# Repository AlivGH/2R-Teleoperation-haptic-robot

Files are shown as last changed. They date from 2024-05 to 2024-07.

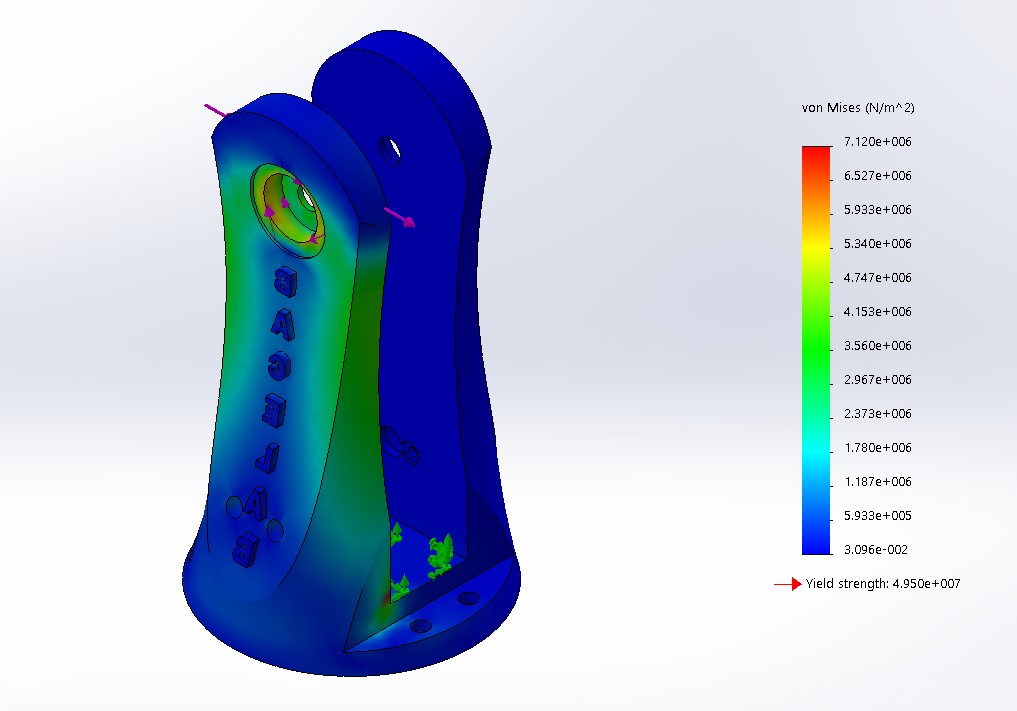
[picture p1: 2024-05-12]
Pictures/0-Tension-v2.jpg

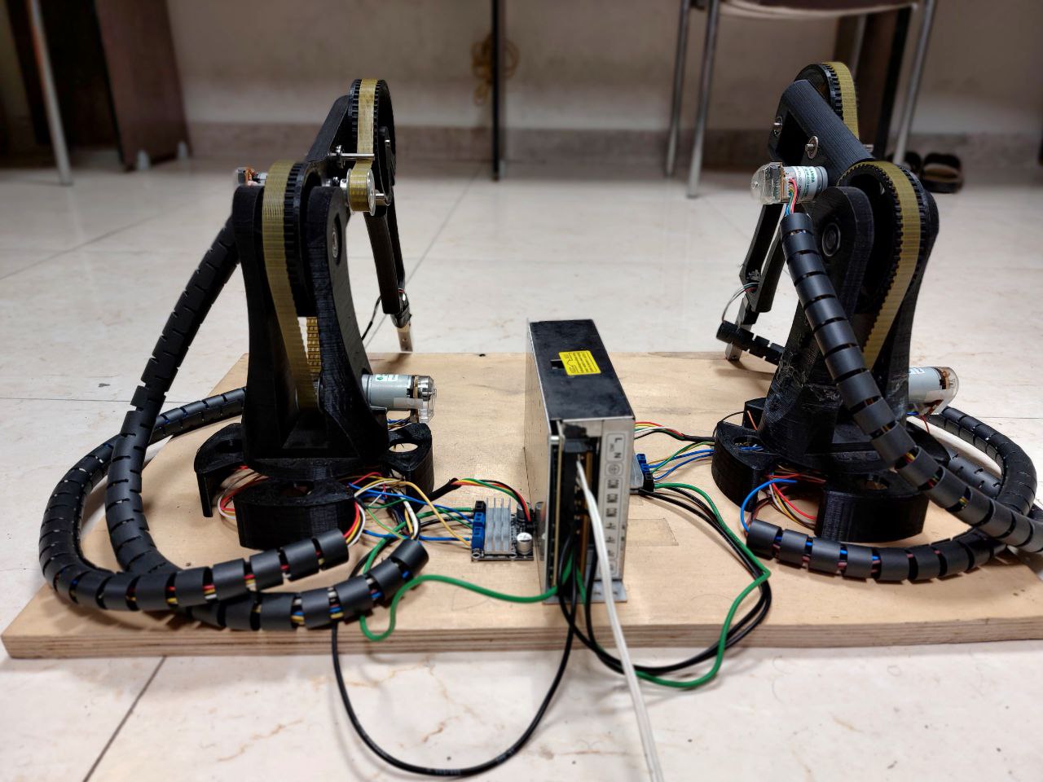
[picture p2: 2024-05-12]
Pictures/photo_5789467008948092437_y.jpg

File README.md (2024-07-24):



# Project Overview

Welcome to my GitHub repository! 🚀 Currently available haptic/teleoperation frameworks either are expensive, provide low-range haptic feedback, or lack sufficient rotational degrees of freedom. To tackle these drawbacks, this project introduces an economical teleoperation setup, including two robots serving as master and slave. The system is actuated by encoder-equipped DC motors, and the applied forces are measured by load cells at the end effectors of the robots. ESP WROOM-32D boards are also used for time-delayed wireless communication. 

The manipulators are first designed in SolidWorks and then printed using a 3D printer. Stress and deformation analyses under a 5-kg load are also provided. The cost-effectiveness of the proposed system is highlighted by reporting the relatively low manufacturing costs. Furthermore, the technical specifications of our framework demonstrate its appeal as an alternative to current haptic devices, offering affordability and versatility.

In this project, basic electrical and mechanical aspects (design, analysis, and manufacturing) are reviewed. For additional information, you can refer to my paper titled “[Cost-effective Haptic Teleoperation Framework: Design and Implementation](https://www.researchgate.net/publication/377825397_Cost-effective_Haptic_Teleoperation_Framework_Design_and_Implementation).”

## Key Skills

- Robotics 💻
- Design 🧠
- 3D Printing 🛠️
- SolidWorks

## Contact Information

Feel free to reach out to me via:

📫 Email: [alivghasemi@gmail.com](mailto:alivghasemi@gmail.com)

✏ LinkedIn: [Ali Ghasemi](https://www.linkedin.com/in/alivghasemi/)

Thank you for exploring my project! 🙌 Your feedback and contributions are highly appreciated. Let's continue pushing the boundaries of deep learning together! 🚀

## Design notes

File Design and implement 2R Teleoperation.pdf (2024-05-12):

## Design and implement

## a 2R Teleoperation haptic robot

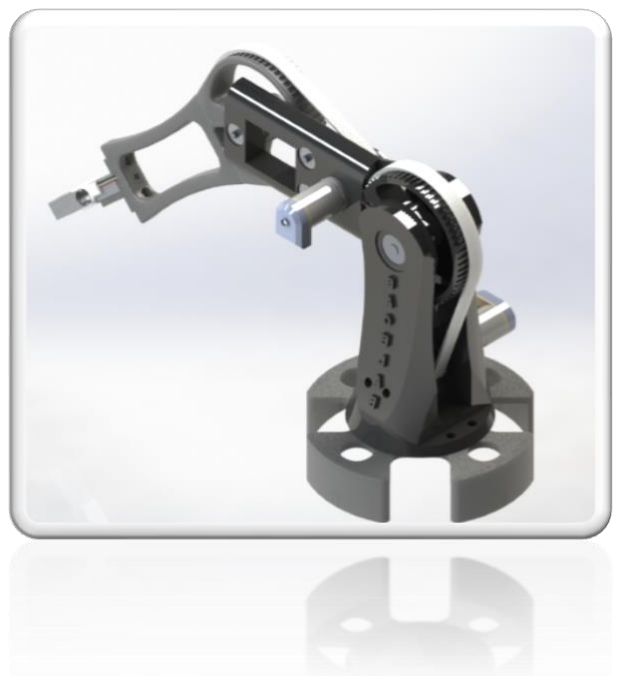
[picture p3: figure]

Ali Ghasemi

Mechanical Engineering Student

Research Enthusiast in Robotics and AI

Iran University of Science and Technology

Contents

## Abstract

Currently available haptic/teleoperation frameworks either are expensive, provide low-range haptic feedback, or lack sufficient rotational degrees of freedom. To tackle these drawbacks, this paper introduces an economical teleoperation setup, including two robots, serving as master and slave. The system is actuated by encoder-equipped DC motors, and the applied forces are measured by loadcells at the end effectors of the robots. ESP WROOM-32D boards are also used for time-delayed wireless communication. The manipulators are first designed in SolidWorks, and are then printed using a 3D printer. The stress and deformation analyses under a 5-kg load are also provided. The cost-effectiveness of the proposed system is highlighted by reporting the relatively low manufacturing costs. Furthermore, the technical specifications of our framework demonstrate its appeal as an alternative to current haptic devices, offering affordability and versatility.

In this project, Basic electrical and mechanical aspects (design, analysis, and manufacturing) are reviewed. However, if you are exploring additional information, you can refer to my paper titled “Cost-effective Haptic Teleoperation Framework: Design and Implementation”.

Key Skills: SolidWorks, Design, 3D printing, Robotics

## Introduction

What is haptic teleoperation robot?

A haptic teleoperation robot combines teleoperation with haptic feedback, providing the operator with a sense of touch or force feedback during remote control operations. This means that in addition to controlling the robot's movements remotely, the operator can also feel the forces exerted by the robot on its environment or objects it interacts with.

Haptic teleoperation systems typically involve force sensors or other feedback mechanisms that transmit the forces experienced by the robot to the operator's control interface. This allows the operator to perceive and react to the physical properties of the remote environment, such as the texture of surfaces or the resistance encountered when manipulating objects.

These systems are valuable in various applications, including surgery, where surgeons can remotely perform delicate procedures with a sense of touch, or in tasks involving hazardous environments, where operators can manipulate objects safely from a distance while receiving tactile feedback about the environment.

Overall, haptic teleoperation robots enhance the operator's control and perception, enabling more intuitive and effective remote operation in a wide range of scenarios.

Why we are creating one?

The current availability of affordable haptic devices presents a challenge: they tend to be either too expensive or difficult to reproduce outside specialized laboratories. This lack of affordable options has drawn attention, prompting a call for solutions that offer accessibility without sacrificing quality.

Commercially available haptic devices, while valuable, often come with limitations. For instance, the Phantom Omni device has a restricted force range, making it less suitable for tasks requiring interaction with rigid external environments or providing extensive haptic feedback.

In response to these challenges, there's a growing need for a teleoperation setup that balances affordability with functionality. Many attempts have been made to adapt existing haptic devices like the Novint Falcon due to their cost-effectiveness. However, this approach presents its own hurdles.

The Novint Falcon, though budget-friendly, lacks rotational degrees of freedom crucial for implementing certain teleoperation theories, limiting its applicability. Furthermore, as it's no longer in production, scalability and further development of systems based on it are slowed down.

In light of these limitations, our objective is to develop a teleoperation system that meets the diverse needs of research while remaining cost-effective. Our contribution lies in creating a framework that not only addresses affordability but also offers wide-range haptic feedback, ample workspace, and intuitive operation for the user.

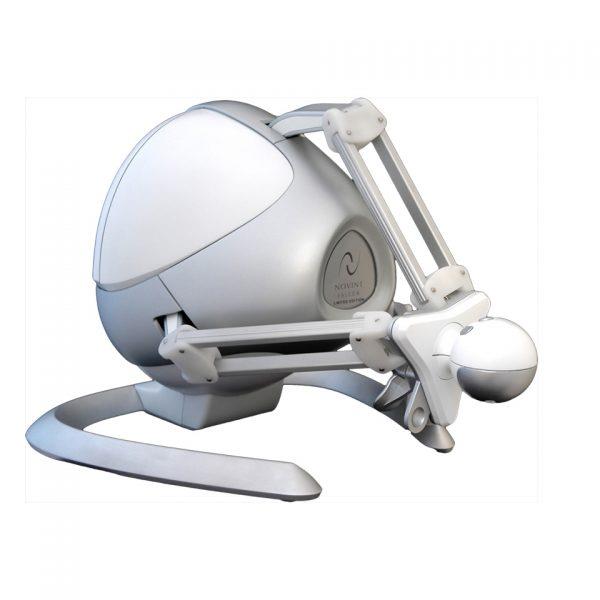
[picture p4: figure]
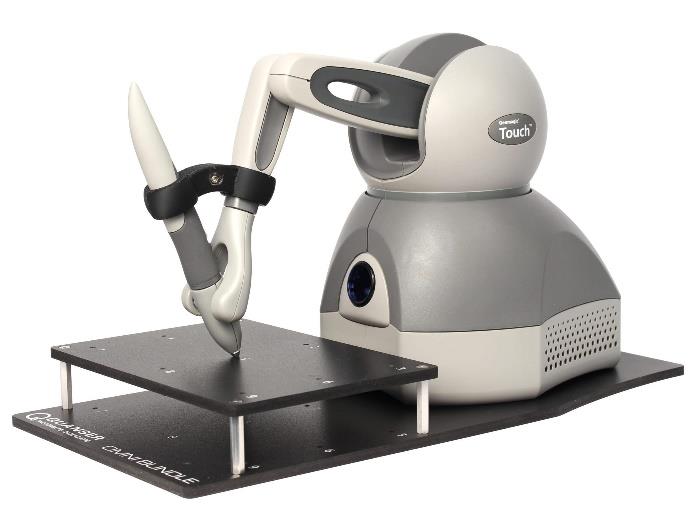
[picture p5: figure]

Figure 1: Falcon Haptic Device | Figure 2: Sensable Phantom

## Design of the system

The main focus of this study is design and construction of two identical 2-DoF robotic arms, the combination of which will form an experimental setup for teleoperation. We started designing the links in SolidWorks considering making the setup as light as possible. The examination of the system’s inertia is an outstanding concern, due to the significant disadvantages associated with excessive mass. To begin with, as the system becomes heavier, it requires more torque from the motors, which increases the overall setup cost. In addition, a heavier setup presents challenges in moving the master robot for the operator. To address this, we removed any surplus material in areas where it was considered unnecessary, ensuring the structural strength remains unquestioned. Furthermore, we determined the length of the links in a way to provide adequate workspace coverage without being overly large which results in mass increasing. The engineering drawings of the links for one robot are shown in Fig. 3. The 3D view of the assembled robot in SolidWorks is also shown in Fig. 4.

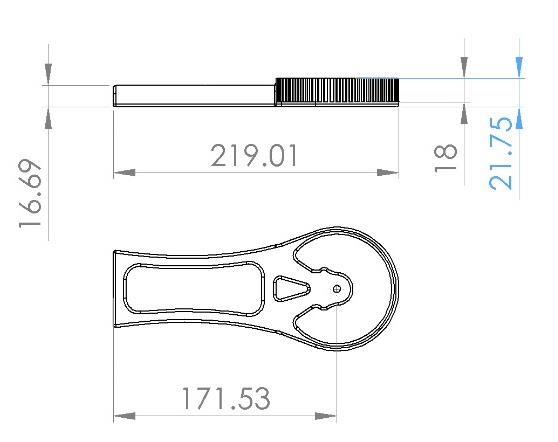
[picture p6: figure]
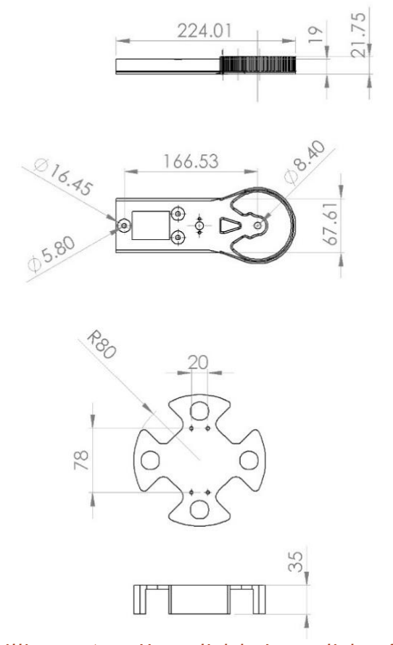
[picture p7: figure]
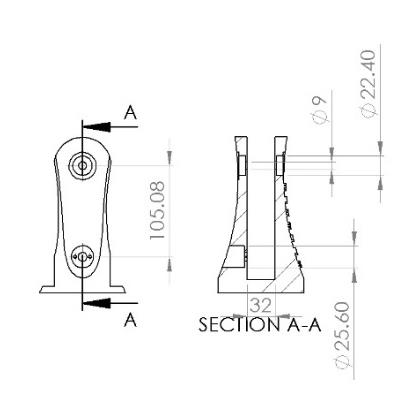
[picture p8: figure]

Figure 3: Drawings of the links of each robot (dimentions are in millimeters): a. Upper link b. Lower link c. Base link d. Base of the robot.

Due to the fact that all links will be produced using BACE lab’s 3D printer, it is essential to acknowledge and account for any constraints and limitations inherent to the printer.

To accommodate the installation of 2 DC motors, two circular empty spaces are incorporated into the robot base and lower link, with essential supports embedded within.

Given the high speed of our motors, power transmission is achieved through a combination of belts and gears. The gear ratio of 1/5 ensures that for every 5 rotations of the pulleys and motors, there is 1 rotation in the subsequent link. This results in the conversion of undesired high speed into torque, enabling a wider range of haptic forces.

As belts are utilized, it is imperative to ensure proper tension. To achieve this, shafts and ball bearings are employed.

The load cell is a vital component of the setup. We have developed a new T-shaped 3D element, called the load cell holder, which securely fastens the 5kg load cell to the robot link. This allows for precise measurement of the force applied on the slave robot, with feedback relayed to the master to mitigate potentially damaging effects.

Links are interconnected using shafts and ball bearings, enabling convenient movement with minimal friction.

In addition to the base support and two links, a base is provided beneath all parts for three primary reasons. Firstly, it elevates the entire setup, facilitating a broader range of operations. However, this elevation also introduces additional safety considerations. Secondly, with the inclusion of electrical units, providing a designated space minimizes confusion associated with complex wiring. Lastly, this base also lays the groundwork for expanding Degrees of Freedom (DoFs) to 3R, enhancing the versatility of the system.

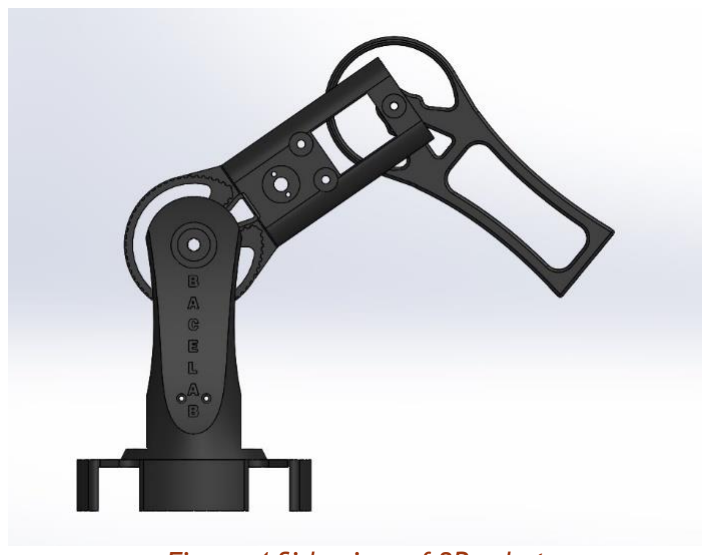
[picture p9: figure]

Figure 4 Side view of 2R robot

## Analysis of the system

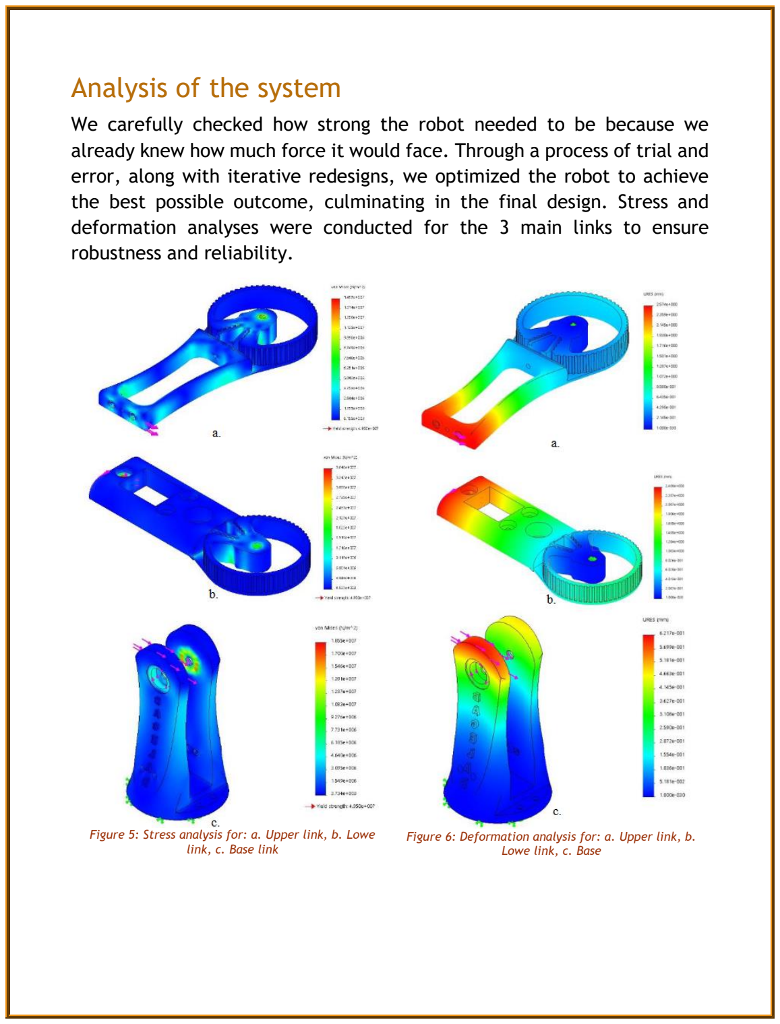
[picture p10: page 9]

We carefully checked how strong the robot needed to be because we already knew how much force it would face. Through a process of trial and error, along with iterative redesigns, we optimized the robot to achieve the best possible outcome, culminating in the final design. Stress and deformation analyses were conducted for the 3 main links to ensure robustness and reliability.

Figure 5: Stress analysis for: a. Upper link, b. Lowe link, c. Base link

Figure 6: Deformation analysis for: a. Upper link, b. Lowe link, c. Base

## Manufacturing of the system

Print Parts

In the beginning we start with printing components. We are using BACE lab 3D printer built by students and this printer use PLA(Polylactic Acid) as Material. To make G-code and also determine mechanical properties “UltiMaker Cura” Software is used.

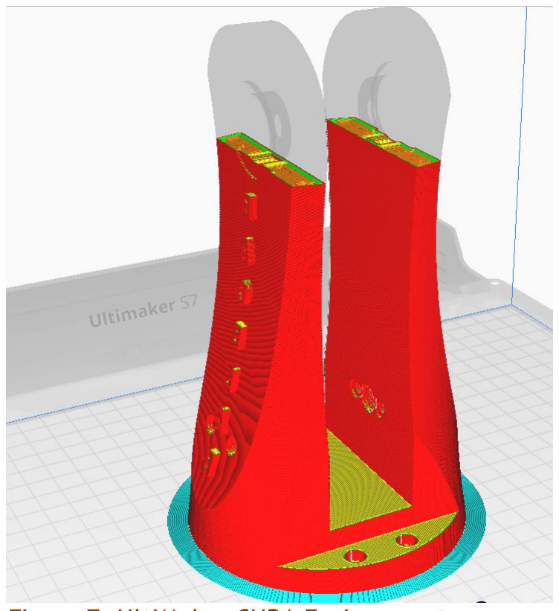
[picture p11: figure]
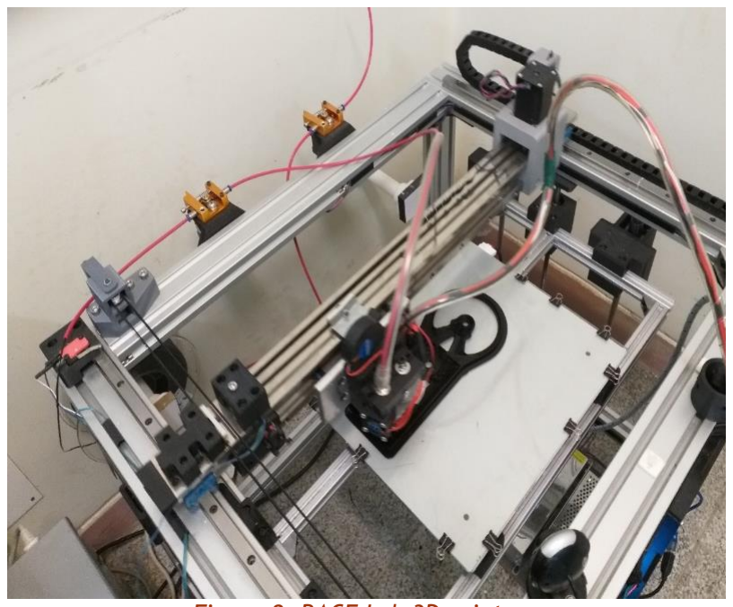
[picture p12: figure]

Figure 7: UltiMaker CURA Environment | Figure 8: BACE Lab 3D printer
All Components Designed in Solidworks Must be exported as <.STL> files. Then, Cura will modify print setting and finally create a G-Code. In the end of this process printer will construct parts. Whole .STL files are placed in GitHub Repository (https://github.com/AlivGH/2R-Teleoperation-haptic-robot) .

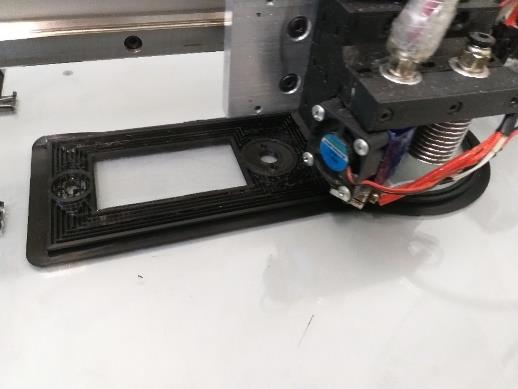
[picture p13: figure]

Figure 9: Printing Link 1

Mechanical properties and bill of material

Properties of designed teleoperation robot is given in following table

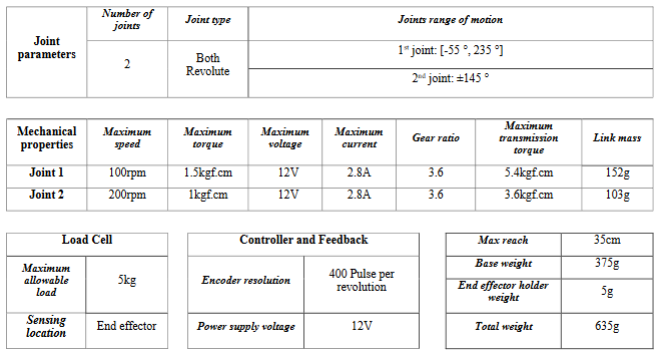
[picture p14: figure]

Other components:

DC Motor Driver | 1
Pulley T5 16teeth | 2
Belt T5 | 2
5mm shaft | 3
8mm shaft | 1
Ball bearing 8*22*7 | 2
Ball Bearing 5*16*5 | 6
Screw | 10 ( suitable size for bore )

Based on Estimation you can attempt to create this robot in USA 50$ and in Iran you can effort 30 million rial.

Setting up links

Base: We accommodated 2 hole for ball bearing and 8mm shaft. Also screw must be used to fix the Dc motor with robot. Pay a lot of attention to this affair. Then put pully on the Motor.

Link1: There are 3 bore in each side for 16mm diameter ball bearing. All 6 ball bearing are to support shafts. 1 shaft linking to next link and 2 utilizing as belt tighten. Put DC motor and then screw it to link. After that place pully on motor shaft.

Link2: 5mm hole to connect to Link1 and 2 holes to connect end effector

Put all together

First of all adjoin belt to links’ gear. Second via 8mm and 5mm shaft make links and base coupled . Then put belt around the pullies and for link 2 and 1 set up belt tighten. Do not forget the end effector and screw it to the holes of link2. Then, locate load cell on it. You also can leverage wire cover and improve the wiring more efficient. Base support can be added to system too.

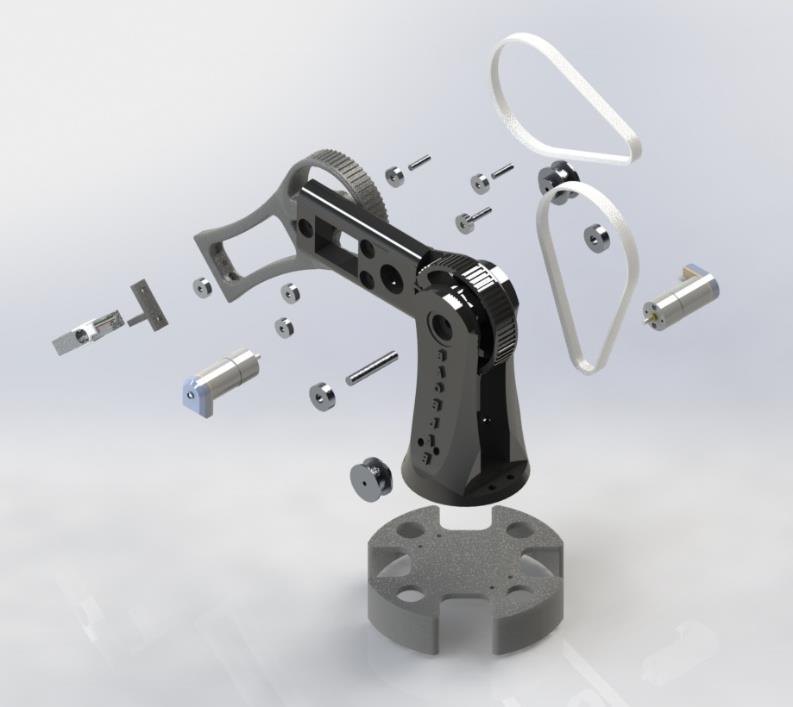
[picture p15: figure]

Figure 10: Exploded View

## Extension To 3R

As mentioned in sections II and III, we have constructed two 2-DoF robotic arms. However, a third degree of freedom can be added to each manipulator so that the three-dimensional space within the workspace of the robots can be reached. Although we have not yet implemented the third DoF, we have conceptualized and designed it in SolidWorks. The scheme of the complete 3-DoF robot is depicted in Fig. 9

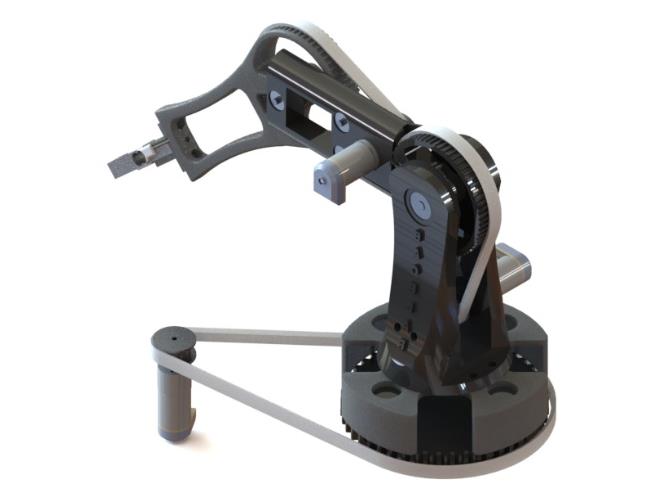
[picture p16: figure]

Figure 11 The 3D view of designed 3-DoF robot

## Make it a Teleoperation Robot

To turn your described robot into a teleoperation robot, you can build two of them and establish a suitable communication protocol. Based on our experience, we recommend using ESP32, which can transmit data through various methods and is cost-effective. Additionally, you'll need a DC motor driver (ZK-BM1), a power supply, wires, and a PerfBoard. You can refer to our paper for detailed methods and results.

## Acknowledge

A heartfelt shoutout to all the members of the Biomechatronic and Cognitive Engineering Lab at IUST, especially

Dr. Borhan Beig Zadeh

Dr. Behnam Yazdan Khoo

Mohammad Yousefi

Kiana Yousefi

Without their advice and generous help, manufacturing this robot would have been impossible. Their contributions were invaluable to the success of this project.

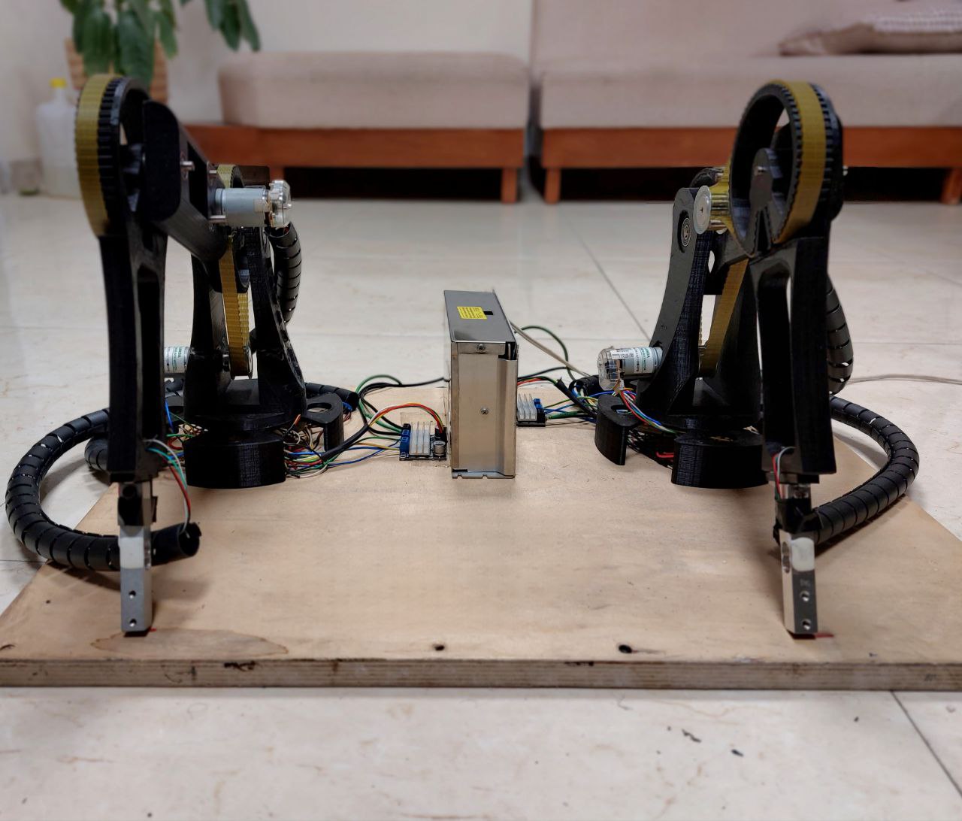
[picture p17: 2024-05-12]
Pictures/photo_5816758060075564648_y (1).jpg

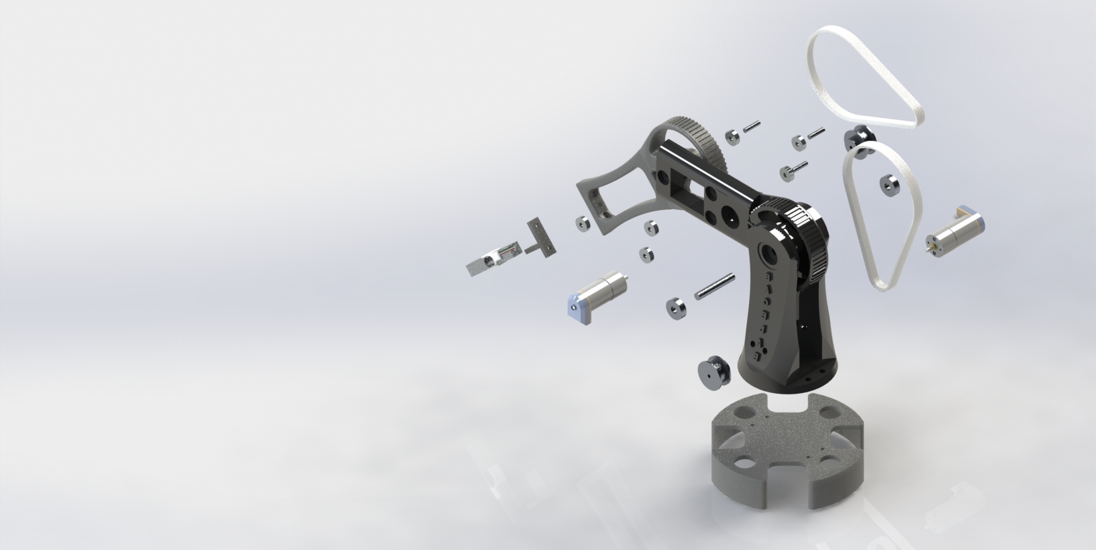
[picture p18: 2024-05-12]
Pictures/Expolded-2R.JPG

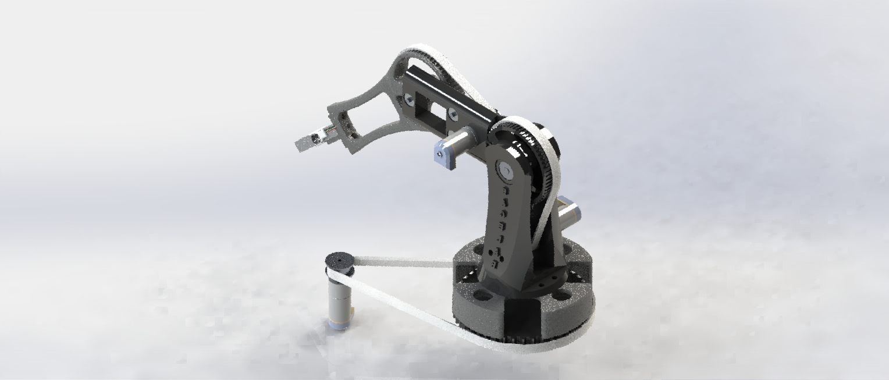
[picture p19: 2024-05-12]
Pictures/preview-3R-V2.JPG

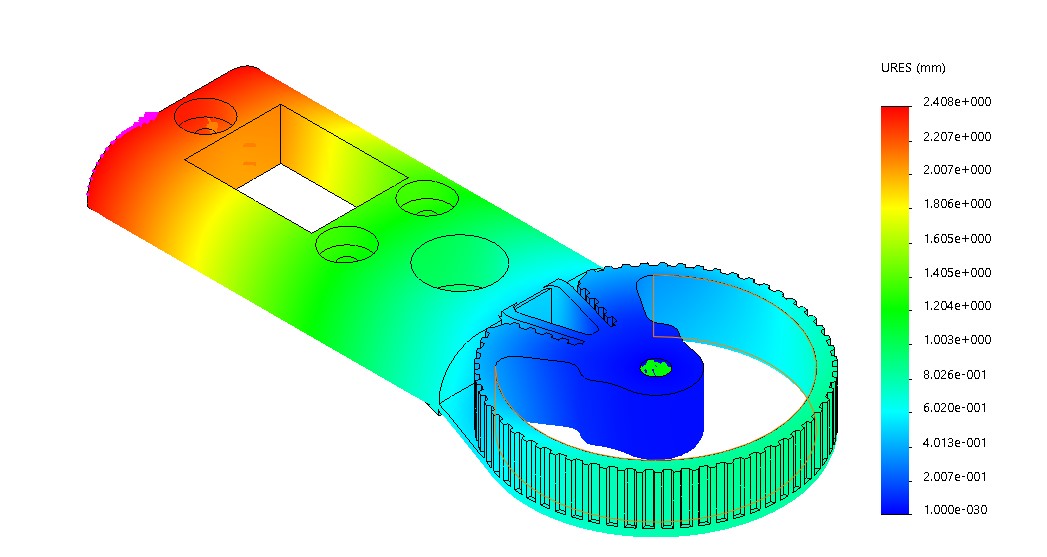
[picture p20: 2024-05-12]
Pictures/1-Strain-v3.jpg

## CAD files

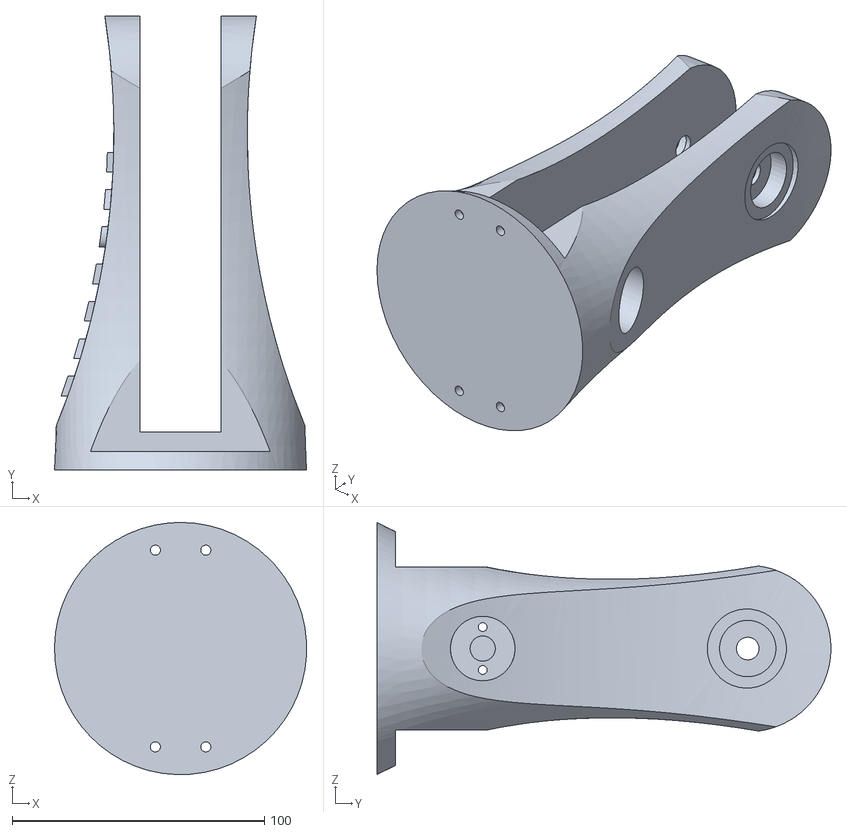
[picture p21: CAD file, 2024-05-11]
STL Files/Base.STL
99.9 x 180.0 x 100.0

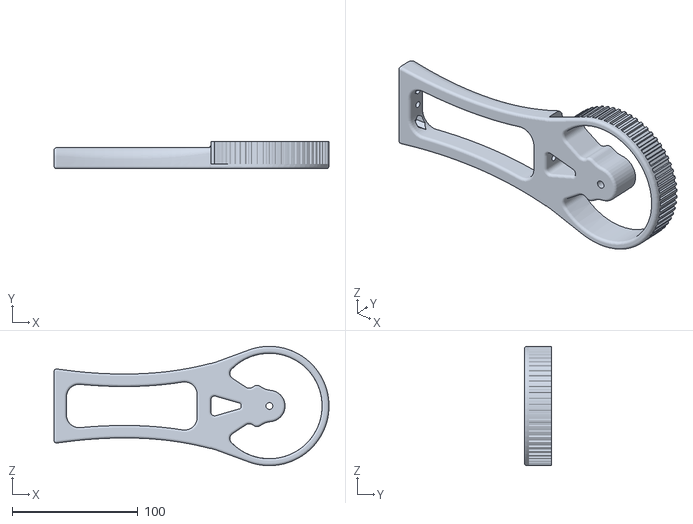
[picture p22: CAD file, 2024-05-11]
STL Files/Link2.STL
219.0 x 21.8 x 95.0

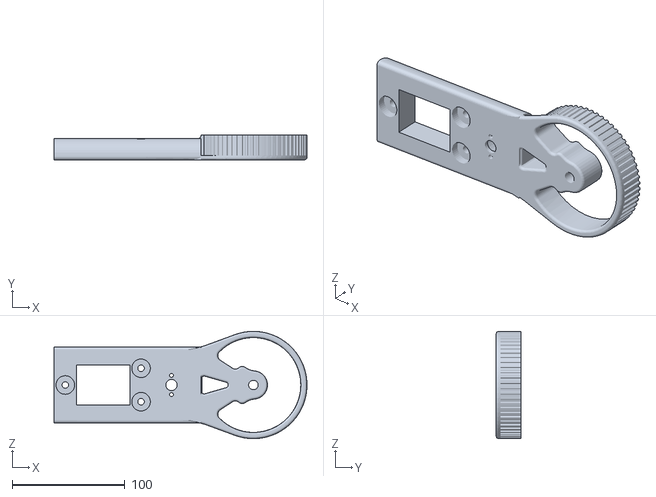
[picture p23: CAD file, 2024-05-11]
STL Files/Link1.STL
224.0 x 21.8 x 95.0

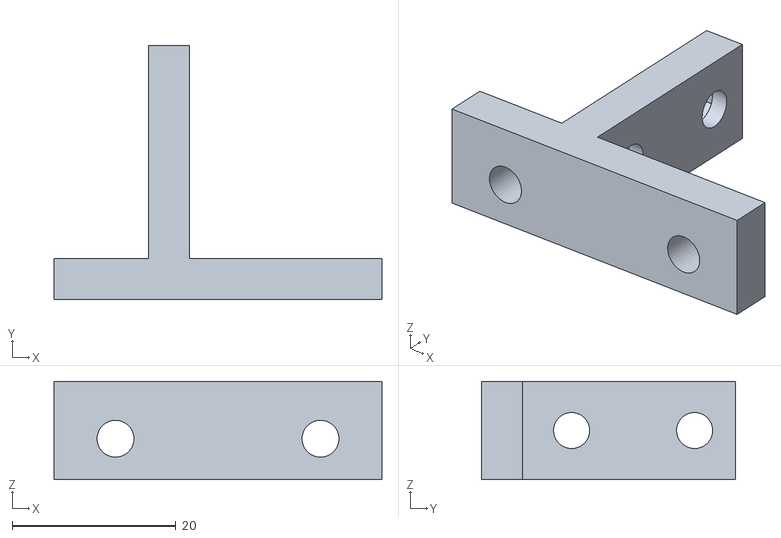
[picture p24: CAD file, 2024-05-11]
STL Files/End effector.STL
40.0 x 31.0 x 12.0

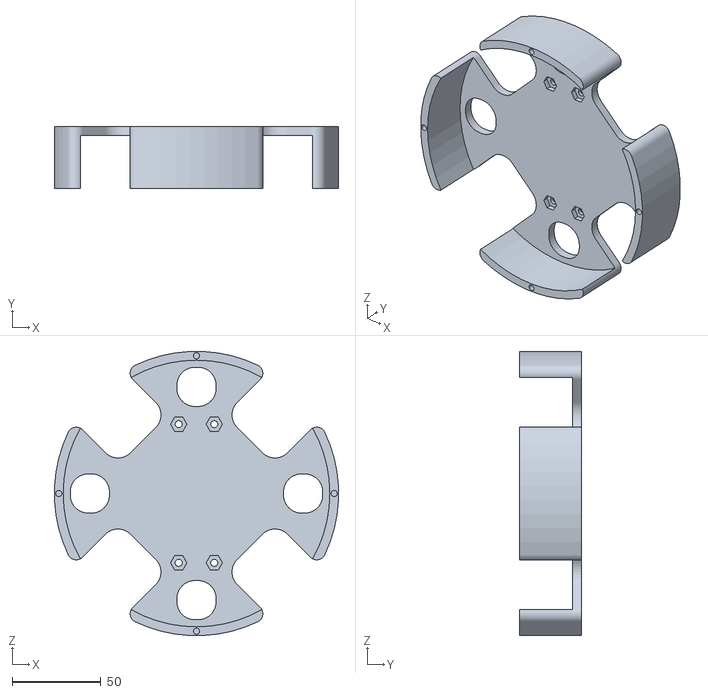
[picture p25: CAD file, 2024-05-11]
STL Files/Base support.STL
159.8 x 35.0 x 159.8

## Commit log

2024-05-11 Add STL files
    [Base support.STL, Base.STL, End effector.STL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]
2024-05-11 Create Thank you for exploring my project! 🙌 Your feedback and contributions are highly appreciated. Let's continue pushing the boundaries of deep learning together! 🚀
